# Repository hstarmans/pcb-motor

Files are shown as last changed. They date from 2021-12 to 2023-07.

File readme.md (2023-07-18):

# PCB Motors

Packages to generate a PCB motor, Carl Bugeja style, for KiCad using Python

## History

Carl Bugeja shared several projects where eletric motors are made directly using PCBs,
see [Hackaday](https://hackaday.io/CarlBugeja) and [Youtube](https://www.youtube.com/c/CarlBugeja).
Drawing these circuits can be a pain. This scripts automates the fabrication.
The scripts only supports Archimidean spirals. Trapezoids are a more popular choise and most likely work better.
An implementation/plugin for kicad can be found [here](https://github.com/atomic14/kicad-coil-plugins).

## Install
Install poetry and python
```console
sudo apt install python3 python3-pip
curl -sSL https://raw.githubusercontent.com/python-poetry/poetry/master/get-poetry.py | python3 -
```
Use poetry to install the dependencies in pyproject.toml
```console
poetry install
```
Change parameters in the script and run it
```console
poetry run python spiral.py
```
The script modifies the base_kicad_pcb and creates a spiral.kicad_pcb.
This can be opened with KiCad and should contain the motor.
This design can be attached to another pcb via Kicad PCB import method.
This feature is only available if KiCad PCB is run in standalone mode. Disable the rat's net before doing so.
At the moment, the user still needs to add connect the coils using the via's.  
It can also be useful to change set the net to the same number as the one you plan to use in the final layout.

## Working of the motor

The magnetic field of a circular ring is shown below;
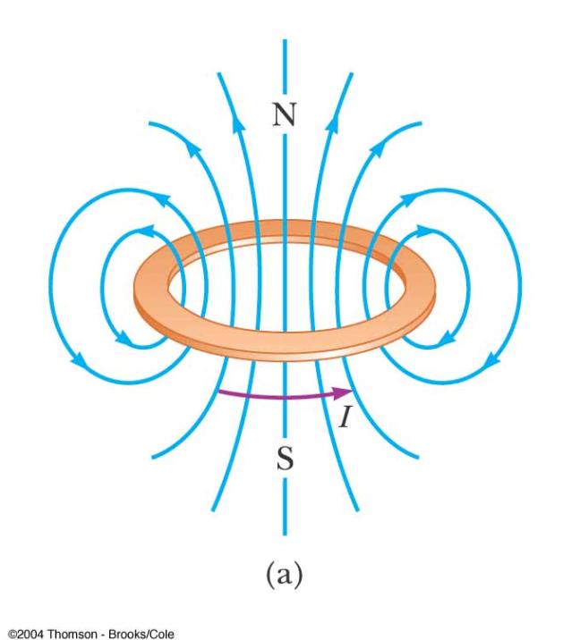
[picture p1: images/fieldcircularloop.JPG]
fieldloop
.
The commutation and switching of motor is outlined [here](https://www.mathworks.com/help/mcb/ref/sixstepcommutation.html).  A [pancake motor](https://www.motioncontroltips.com/faq-servo-pancake-motors-work/) provides an alternative implementations of a PCB motor.  It was not used as there is no open source design available.

## Ideal number of stator magnets
The optimal number of magnets can be found from this document and goes into depth in the winding factor
https://things-in-motion.blogspot.com/2019/01/selecting-best-pole-and-slot.html.
The information is based off the paper 'Distribution, coil-span and winding factors for PM machines with concentrated windings' by S.E Skaar et al. and the book 'Design of Brushless Permanent-magnet Machines' by J. R. Hendershot and T. Miller. See the 'recommended reading' list above for more information on this book. The emotor.com glossary page is also useful for reference.

## Packing of circles on a circle
https://math.stackexchange.com/questions/942775/how-many-circles-with-radius-r-1-can-be-inscribed-in-circle-with-radius-r-2

## Some facts & equations
Standard grade neodymium magnets have a maximum operating temperature of 80 degrees [Celsius](https://www.magnetexpert.com/technical-advice-for-every-application-magnet-expert-i685/temperature-effects-on-magnets-i683).  
Force between two magnets follows a square [law](https://en.wikipedia.org/wiki/Force_between_magnets), ideally the PCB is thin!  
Heat generated by the PCB equals $P=R \cdot I^2$, here P is power, I is current and R is resistance of the coil.  
  
The resistance of a PCB trace is;  
$R = \frac{\rho L}{T W}(1 + \alpha (T_{amb} – 25))$   
Here, R is the resistance; L is the length of the trace; T is the thickness of the trace;
W is the width of the trace and Tamb is the ambient temperature in Celcius.
Alpha is the resistivity of copper which is 0.39 percent for each [degree](https://www.cirris.com/learning-center/general-testing/special-topics/177-temperature-coefficient-of-copper).  
Torque is defined as $\tau = F \cdot R$, if the magnets are further away from the center you can excert more force. 
The magnetic field produced at the centre of a current-carrying coil of 𝑁 turns is;  
$B=\frac{\mu N I}{2R}$, here 𝐼 is the current in the solenoid, $\mu$ is the magnetic permeability and R is the [radius](https://physics.stackexchange.com/questions/355140/magnetic-field-due-to-a-coil-of-n-turns-and-a-solenoid).

## Results

Script creates a 4 layer PCB motor with 6 poles.
The front copper layer is shown below,  
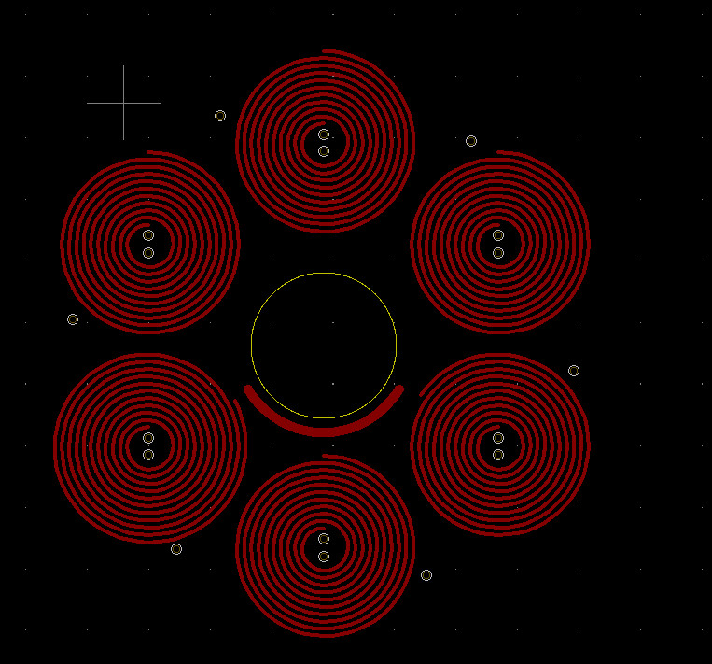
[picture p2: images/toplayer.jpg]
toplayer
  
The In1.Cu layer is shown below. The style of these connections is named "Carl Bugeja" styled PCBs.  
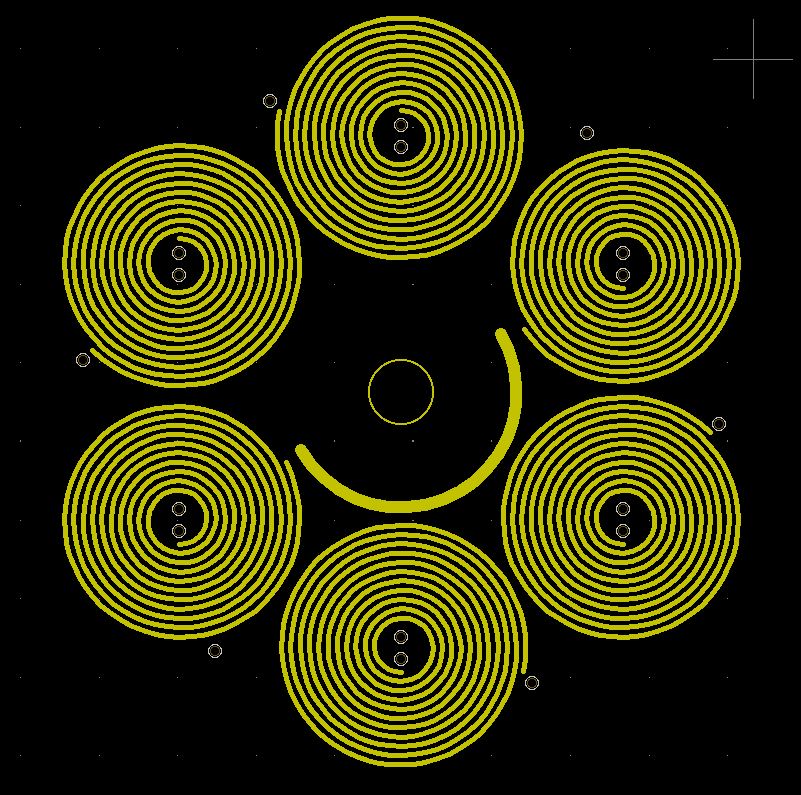
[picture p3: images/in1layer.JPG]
layer1
  

## Video

A voltage of 5V was applied over the board. The current reached 0.7 amps. Over time the temperature of the
board stabilized at 60 degrees Celcius.

Watch the video (https://youtu.be/r3wv7XpXPck)

## Control software

Gateware to pulse the motor can be found [here](https://github.com/hstarmans/hexastorm/tree/master/tests/custommotor).

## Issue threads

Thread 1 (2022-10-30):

video link? number of magnets in rotor?

aewallin, 2022-10-30:
Hi, nice project! The readme has a link to a video, but it seems broken.
Found some videos on your youtube-channel, maybe you can link to one of those?

In your videos you have this coil-PCB with 6 coils, and the rotor has 4 magnets.
is that optimal? or would it work with 5 or 6 magnets also?

hstarmans, 2022-10-31:
Video link should be fixed now.
No it is not optimal. Carl bugeja designed special magnets. He uses a metal encasing and 10 magnets see https://youtu.be/zeGKYIcLMIs?t=1186. He ordered this via ali express. The metal encasing enhances the field, this is known from pot magnets. He indeed seems to use a triangular style segment. So probably my archimedean spiral design is sub optimal.
The optimal number of magnets can be found from this document
 https://things-in-motion.blogspot.com/2019/01/selecting-best-pole-and-slot.html

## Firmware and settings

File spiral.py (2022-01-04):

import numpy as np

def segment(start, end, width, layer, net):
    '''draws segment from start to end

        start: start point of track, list
        end: end point of track, list
        width: width of line
        net: net used
        layer: layer line is drawn upon
    '''
    text = f"(segment (start {start[0]:6f} {start[1]:6f}) (end {end[0]:6f}  {end[1]:6f})"
    text += f" (width {width}) (layer {layer}) (net {net}))\n"
    return text


def graphic_circle(center, radius, layer, width=0.05):
    ''' draws graphic circle as position with radius at layer with width
    '''
    text = f"(gr_circle (center {center[0]} {center[1]}) (end {center[0]} {center[1]+radius})"
    text += f"(layer {layer}) (width {width}))"
    return text

def arc(center, radius, startangle, finalangle, track_dct, segs=20):
    '''draws circular arc with center radius, start- and finalangle

        radius: radius of arc
        start angle: start angle of arc
        end angle: final angle of arc
        track_dct: width, net and layer of track, dct
        segs: number of straight semgents used to draw arc
    '''
    segangle = np.radians((finalangle-startangle) / segs)
    str_data = ""

    def circle_formula(i):
        angle = segangle*i+np.radians(startangle)
        return np.array([np.sin(angle), np.cos(angle)])*radius

    for i in range(int(segs)):
        start = center + circle_formula(i)
        end = center + circle_formula(i+1)
        str_data += segment(start.tolist(), end.tolist(), **track_dct)
    return str_data


def archimidean_spiral(center, start_radius, track_distance,
                       start_angle, final_angle, turns, rotation,
                       track_dct, segments=20):
    '''draws spiral arc with center radius, start and finalangle

        radius: start radius of spiral
        track_distance: distance between tracks
        start angle: start angle of spiral
        final angle: final angle of spiral
        turns: number of turns in spiral
        rotation: rotation vector points toward screen, boolean
        track_distance: distance between tracks
        track_dct: settings for track
        segs: number of straight semgents used to draw arc
    '''
    str_data = ""
    # track distance should account for track width
    track_distance += track_dct['width']
    for j in range(turns):
        # each turn consists of more segments
        # and a smaller angle angle per segment
        segments += 4
        segangle = 360.0 / segments
        segradius = track_distance / segments

        if j == turns-1:
            segments = int(final_angle/360*segments)

        def spiral_formula(i):
            angle = np.radians(segangle*rotation*i + start_angle)
            return ((start_radius + segradius * i + track_distance*(j+1))
                    *np.array([np.sin(angle), np.cos(angle)]))

        for i in range(segments):
            # central rings for HV and SNS
            start = center + spiral_formula(i)
            end = center + spiral_formula(i+1)
            str_data += segment(start.tolist(), end.tolist(), **track_dct)

    return str_data

def drill_via(position, size=0.45, drill=0.3, net=0):
    '''drill via of size with dril in net
    '''
    text = f"(via (at {position[0]:6f} {position[1]:6f}) (size {size})"
    text += f" (drill {drill}) (layers F.Cu B.Cu) (net {net}))\n" 
    return text

def archimedian_spiral_outer_radius(turns, track_width, track_distance, start_radius):
    ''' gives estimate of outer radius archimedian spiral 

        turns: number of turn in spiral
        track_width: width of track
        track_distance: distance between tracks
        start_radius: starting radius of archimedian spiral
    '''
    return (turns+1)*(track_width+track_distance) + start_radius


def four_layer_coil(center, top_angle, connect_angle, bottom_angle, rotation,
                    layer_stack, spiral_dct, track_dct):
    '''draws coil in electric pcb motor

       an electric motor consists of multiple coils in a circular pattern around
       a center. This coil consists out of four layers.
       Current can enter and exit the coil at the first and second layer.
       The entry angle of the first layer is known as the top angle
       The entry angle of the last layer is known as the bottom angle
       The via which connects layer 2 and 3 is placed at connect angle.

       center: center of coil, list
       top_angle: entry angle of first layer, float
       connect_angle: location of via between 2 and 3 layer, float
       bottom_angle: exit angle of final layer, float
       layer_stack: layers used to draw coils on, list
       spiral_dct: settings for spiral
       track_dct: settings for tracks

        returns String which can be read by KiCad PCB
    '''
    # vias to connect coils

    # vias of inner ring
    pos_hole = center + np.array([0, 0.35])
    res = drill_via(pos_hole)
    pos_hole -= np.array([0, 0.7])
    res += drill_via(pos_hole)
    # vias from outer ring
    radius = archimedian_spiral_outer_radius(spiral_dct['turns'],
                                             track_dct['width'],
                                             spiral_dct['track_distance'],
                                             spiral_dct['start_radius'])                                             
    # some additional offset to not touch tracks
    radius += 0.3
    
    angle = np.radians(90-connect_angle)
    pos_hole = center + radius * np.array([np.cos(angle), -np.sin(angle)])
    res += drill_via(pos_hole)
    spiral_dct['center'] = center
    # layer 0
    spiral_dct['start_angle'] = 180
    spiral_dct['rotation'] = 1*rotation
    spiral_dct['final_angle'] = top_angle
    track_dct['layer'] = layer_stack[0]
    res += archimidean_spiral(**spiral_dct, track_dct=track_dct)
    # layer 1
    spiral_dct['start_angle'] = 180
    spiral_dct['rotation'] = -1*rotation
    spiral_dct['final_angle'] = (connect_angle*rotation+360)%360
    track_dct['layer'] = layer_stack[1]
    res += archimidean_spiral(**spiral_dct, track_dct=track_dct)
    # layer 2
    spiral_dct['start_angle'] = 0
    spiral_dct['rotation'] = 1*rotation
    spiral_dct['final_angle'] = (180-connect_angle*rotation+360)%360
    track_dct['layer'] = layer_stack[2]
    res += archimidean_spiral(**spiral_dct, track_dct=track_dct)
    # layer 3
    spiral_dct['start_angle'] = 0
    spiral_dct['rotation'] = -1*rotation
    spiral_dct['final_angle'] = bottom_angle
    track_dct['layer'] = layer_stack[3]
    res += archimidean_spiral(**spiral_dct, track_dct=track_dct)
    return res


def pcb_motor(position, axis_radius, spiral_dct, track_dct, coil_dct):
    '''draws Carl Bugeja styled PCB motor at position

    pcbmotor has 6 coils and 4 layers
    connection between poles is done via the center and using 
    different layer stacks per coil
    user still has to draw the final connections
    
    position: position of PCB motor
    axis_radius: radius of central axis of PCB motor
    spiral_dct: settings for spiral in coils, dct
    coil_dct: settings for coil, dct
    track_dct: settings for tracks, dct
    '''
    
    poles = 6                        # poles of motor
    angle_included = 2*np.pi/poles   # included angle
    outer_radius = archimedian_spiral_outer_radius(spiral_dct['turns'],
                                                   track_dct['width'],
                                                   spiral_dct['track_distance'],
                                                   spiral_dct['start_radius'])   
    # safety margin
    outer_radius += spiral_dct['track_distance']/4
    # https://math.stackexchange.com/questions/134606/distance-between-any-two-points-on-a-unit-circle
    radius_motor = (2*outer_radius)/(2*np.sin(angle_included/2))


    # layer stack for each pole
    stacks = [['F.Cu', 'B.Cu', 'In1.Cu', 'In2.Cu']]
    stacks += [['F.Cu', 'In2.Cu', 'In1.Cu', 'B.Cu']]
    stacks += [['F.Cu', 'In2.Cu', 'B.Cu', 'In1.Cu']]
    stacks += [['F.Cu', 'In1.Cu', 'B.Cu', 'In2.Cu']]
    stacks += [['F.Cu', 'In1.Cu', 'In2.Cu', 'B.Cu']]
    stacks += [['F.Cu', 'B.Cu', 'In2.Cu', 'In1.Cu']]
    
    str_data = ""
    for pole in range(poles):
        angle = angle_included*pole +angle_included/2
        coil_center = position + np.array([np.cos(angle), np.sin(angle)])*radius_motor
        # top poles of motor should connect to phases
        if pole >= 3:
            coil_dct['top_angle'] = 0
            coil_dct['rotation'] = 1
            coil_dct['bottom_angle'] = (np.degrees(angle_included)*(2+pole)+360)%360
        else:
            coil_dct['top_angle'] = (np.degrees(-angle_included)*(1-pole)+360)%360
            coil_dct['bottom_angle'] = (np.degrees(-angle_included)*(2+pole)+360)%360
            coil_dct['rotation'] = -1
        coil_dct['center'] = coil_center
        coil_dct['connect_angle'] = (45+np.degrees(angle_included)*pole + 360)%360
        coil_dct['layer_stack'] = stacks[pole]
        str_data += four_layer_coil(**coil_dct, spiral_dct=spiral_dct, track_dct=track_dct)

    # center hole for slide bearing
    str_data += graphic_circle(position, axis_radius, 'Edge.Cuts')

    # connections between poles
    track_dct['width'] = 0.4
    track_dct['layer'] = 'In2.Cu'
    tracks_radius = radius_motor-outer_radius-0.4
    str_data += arc(position, tracks_radius, +np.degrees(angle_included), 
                    180+np.degrees(angle_included), track_dct)
    track_dct['layer'] = 'B.Cu'
    str_data += arc(position, tracks_radius, 0, 180, track_dct)
    track_dct['layer'] = 'In1.Cu'
    str_data += arc(position, tracks_radius, -np.degrees(angle_included), 
                    180-np.degrees(angle_included), track_dct)
    # triple revert connection
    track_dct['layer'] = 'F.Cu'
    str_data += arc(position, tracks_radius, -np.degrees(angle_included), 
                    np.degrees(angle_included), track_dct)

    return str_data


if __name__ == '__main__':

    track_dct = { "layer": "F.Cu",
                  "net": "0",
                  "width": 0.15}

    spiral_dct = {
        "center": np.array([115.0, 105.0]),
        "start_radius": 0.5,     # mm
        "track_distance": 0.15,  # mm
        "start_angle": 0,         # degrees
        "final_angle": 360,       # degrees
        "turns": 11,
        "rotation": -1}
    
    coil_dct = {
        "center": np.array([115.0, 105.0]),
        "top_angle": 0,       # degrees
        "connect_angle": 45,  # degrees
        "bottom_angle": 360,  # degrees
        "rotation": 1,
        "layer_stack": ['F.Cu', 'In1.Cu', 'In2.Cu', 'B.Cu']
    }
    position = np.array([152.0, 100.0])  # center of motor


    # open base file
    start = None
    end = None
    with open("base.kicad_pcb", "r") as f:
        lines = f.readlines()
        start = lines[:99]
        end = lines[99:]
   
    
    with open('spiral.kicad_pcb', 'w') as f:
        for line in start:
            f.write(line)
        
        str_data = pcb_motor(position, 1.05, spiral_dct, track_dct, coil_dct)
        f.write(str_data)

        for line in end:
            f.write(line)

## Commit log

2021-12-04 fixed bugs due to move to numpy
    [spiral.py]
2021-12-04 added edge cut for center
2021-12-05 connections between poles, correct layer stack
    [spiral.py]
2022-01-04 fixed field of opposing coils
    [spiral.py]
2022-01-04 fixed error with connect
    [spiral.py]
